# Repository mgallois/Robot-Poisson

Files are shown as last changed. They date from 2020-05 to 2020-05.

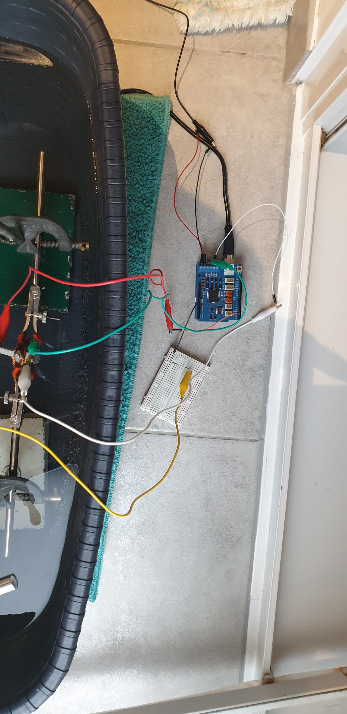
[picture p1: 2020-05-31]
documents tiers/Images/5.jpg

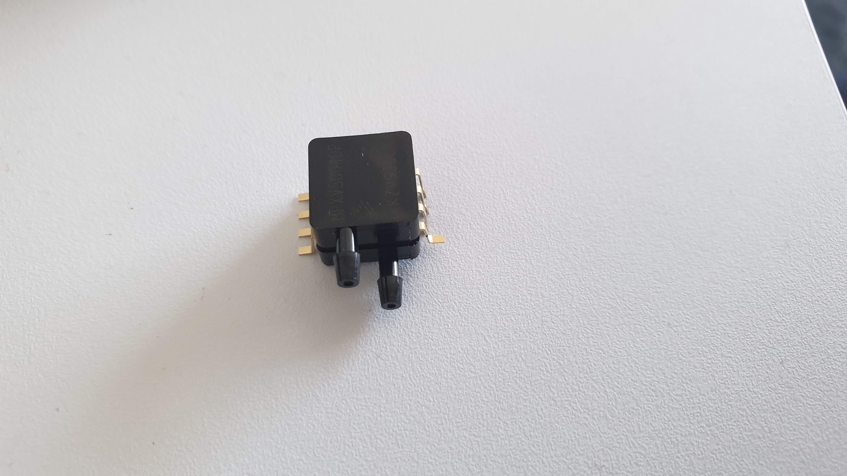
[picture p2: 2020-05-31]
documents tiers/Images/12.jpg

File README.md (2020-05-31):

# Robot-Poisson

INTRODUCTION :

Plusieurs domaines d’applications sont touchés par la nécessité d’entreprendre des prises de vues sous-marines : infrastructures immergées, barrage, pipeline, expertise maritime de bateaux (coques), recherche sous-marine, aquaculture, etc. L’emploi de drones sous-marins a à la fois rendu l’inspection de ces milieux subaquatiques plus simple, rapide et moins coûteuse, et permet d'explorer des fonds marins fragiles sans endommager l'environnement et son écosystème.

Cependant certaines profondeurs sont difficiles d’accès, des engins de faible volume qui embarquent l’énergie nécessaire à la réalisation de leur mission sont alors indispensables. D’où le besoin de systèmes peu énergivore.

Il faut savoir que dans le milieu du XXième siècle, le biologiste Sir James Gray mis en évidence une singularité à qui il donna son nom . Son hypothèse, qui a formé la base de l'analyse énergétique de la nage des dauphins par Gray, était qu'un animal qui nage dépense essentiellement son énergie musculaire pour surmonter la traînée. Or il énonça que la puissance dépensée par un dauphin pour nager à une vitesse donnée peut être sept fois inférieure à celle utilisée par des moteurs pour propulser un corps rigide à la même vitesse, ce qui conduit au paradoxe. [Extrait de sa thèse](https://jeb.biologists.org/content/jexbio/13/2/192.full.pdf).

Ainsi sa conjecture doit être révisé :  la puissance de traînée peut être supérieure à la puissance musculaire sans enfreindre tout principe physique.

Pour expliquer ce phénomène, il faut s’intéresser à la nage du poisson qui fait se propager une onde le long de son corps. On peut associer au déplacement du poisson un nombre de Reynolds correspondant à une allée de tourbillons de Karman. L’action de la queue va déformer cette allée et déplacer les tourbillons de l’autre côté de l’axe de la queue. Cette allée de tourbillons de Karman inversée crée un excès de quantité de mouvement qui entraîne une force propulsive sur le poisson. (Voir [ici](https://github.com/mgallois/Robot-Poisson/blob/master/explication%20rapide%20ph%C3%A9nom%C3%A8ne.md) pour une explication un peu plus détaillé)

Cette démarche biomimétique apparaît prometteuse pour remplacer la traditionnelle hélice de propulsion. L’objet de la robotique biomimétique est de concevoir et fabriquer des machines inspirées de la faune sous-marine, qui ont l’avantage de ne pas effrayer la vie marine contrairement à nos réalisations actuelles. Les premiers prototypes de « robots poissons » sont en développement, voire prêt à la commercialisation tel SoFi conçu par des chercheurs du MIT. C’est un poisson robotique sous-marin non attaché qui peut exécuter de manière autonome des commandes reçues à distance d'un plongeur. Ce projet démontre la possibilité de propulser un drone en imitant la nage d’un poisson.

Notre objectif est de concevoir un robot poisson à la fois souple et adapté à l’immersion. Le poisson robotisé doit se mouvoir à l’aide d’une ondulation biomimétique développant une force de poussée. Il sera question de concevoir, à l’aide de Simon Querat de l’ENS Rennes, un actionneur qui mettra en mouvement une queue moulée en silicone.

Enfin, l’un des défis d’une telle conception est de définir la fonction de déformation de la queue idéale. Son obtention est d’autant plus complexe qu’il fait appel à des notions complexes de mécanique des fluides, dont l’équation de Navier-Stokes qui est non linéaire. Il est cependant possible d’utiliser des modèles informatiques. Ces outils permettent de calculer la résultante des forces s’exerçant sur un corps déformable plongé dans un fluide en écoulement. Le Code utilisé ici est [LilyPad](https://github.com/weymouth/lily-pad).

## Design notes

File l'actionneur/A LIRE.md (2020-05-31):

# Etude de l'actionneur

__Principe de fonctionnement :__

L’objectif est d’agiter la queue du poisson pour qu’ils puisse nager. L’utilisation d’un servomoteur classique nous a semblé compliqué car beaucoup d’entre eux ont un temps de parcourt beaucoup trop long. Nous avons donc décidé d’en concevoir un nouveau :



Comme le montre cette image, l’idée est d’utiliser un aimant permanant qui serait placé à l’intérieur d’une bobine. En faisait circuler un courant dans la bobine, nous créons un couple sur l’aimant. En faisant circuler un courant alternatif, nous pouvons agiter les aimants.

Dans la pratique, nous fixons les aimant dans un cadre imprimé en 3D auquel la queue du poisson pourra venir se fixer :




La commande se fait soit par un montage push pull ([vidéo](https://youtu.be/8bh-lfFtLSA)), soit à l’aide d’une carte arduino ([code](https://github.com/mgallois/Robot-Poisson/blob/master/codes%20divers/code%20arduino/programme_commande_actionneur/programme_commande_actionneur.ino)).

__Mesure du couple transmissible :__

On se propose ici de déterminer expérimentalement le couple transmissible. En effet, nos modèles théoriques sont trop éloignés de la réalité (bobine d’épaisseur non négligeables, champs des aimants irréguliers, etc…).

Afin de mesurer la relation entre le couple et l’intensité, nous accrochons un dynamomètre à l’extrémité de l’actionneur et nous l’alimentons avec un courant continu d’intensité variable. ([Résultats](https://github.com/mgallois/Robot-Poisson/blob/master/l'actionneur/Couple%20Actionneur%20en%20fonction%20de%20l'intensit%C3%A9.xlsx))

__Tracé dans Bode du comportement de l’actionneur :__

L’étude de la réponse se fait par analyse vidéo. Cette étape est pour le moment en suspend.([ebauche tableur](https://github.com/mgallois/Robot-Poisson/blob/master/l'actionneur/trac%C3%A9%20dans%20bode%20(%C3%A9bauche).xlsx)).

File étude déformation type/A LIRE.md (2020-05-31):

INTRODUCTION

Le but de cette étude est de déterminer la géométrie que la queue en silicone devra satisfaire. Concernant la forme globale, il s’agira d’un profil Nacca.

Objectifs :

*	Déterminer les déformations possibles pour une queue déformable agité à son extrémité
*	Simuler à l’aide de Lilypad la poussé de chaque déformation puis déterminer la plus efficace.
*	Estimer les besoins en alimentation de l’actionneur et la taille maximale de la queue pour satisfaire à la déformation choisie et pour atteindre une fréquence de l’ordre de 2 ou 3 Hz.

I_ DETERMINER LES DEFORMATIONS POSSIBLES ET SIMULATION

Nous observons la déformation d’une feuille de papier de fort grammage (300g.m-2) soumise à une excitation sinusoïdale à l’une de ses extrémités :



En fonction de la fréquence, nous obtenons différentes déformation types. Nous pouvons ensuite utiliser Lylipad pour déterminer à quelle vitesse se déplacerait un profil Nacca qui aurait ces déformations. Le profil Nacca utilisé correspond à la forme prévue dans [ce fichier](https://github.com/mgallois/Robot-Poisson/blob/master/Plans/mod%C3%A8le%20de%20queue.SLDPRT).

NB : Comparer directement ces vitesses n’aurait pas beaucoup de sens. En effet, il est évident que plus la fréquence de nage est élevée, plus un poisson ira vite. C’est pourquoi dans la simulation nous ne changeons pas la fréquence de la nage, mais seulement la déformation en elle-même. Par défaut, nous appliquons une fréquence de 3Hz à la simulation.

[vidéo de l'expérience](https://github.com/mgallois/Robot-Poisson/blob/master/%C3%A9tude%20d%C3%A9formation%20type/vid%C3%A9o%20d%C3%A9formation.mp4) (fréquence de 1Hz à 15Hz avec un pas de 1Hz toute les 10 secondes).

| Fréquence d’agitation de la feuille de papier (en Hz) | Vitesse simulée Avec lilypad (en cm.s-1) |
| :---:| :---: |
|1|0,6|
|2|1,2|
|3|1,0|
|4|0,9|
|5|1,0|
|6|0,8|
|7|0,8|
|8|0,7|
|9|0,6|
|10|0,6|
|11|0,5|

Nous obtenons ainsi un objectif de déformation à atteindre.

Une seconde simulation montre que plus la queue est grande, plus la propulsion est efficace. Nous chercherons donc à avoir la plus grande queue possible.

II_ BESOINS EN ALIMENTATION ET TAILLE MAXIMALE
	 
HYPOTHESE 1 : L’épaisseur de la queue influe peut sur le couple résistant devant la surface exposée : on peut donc utiliser une plaque de même surface que la queue.

HYPOTHESE 2 : Au vue de la déformation choisie, une plaque de PVC légèrement déformable apporte une estimation suffisamment proche du couple résistant. 

Les plaques en PVC correspondent aux différentes tailles de queue envisagées. Nous ne nous attarderons pas sur des calculs d’inertie, de couple résistant, etc. Comme nous cherchons à atteindre une fréquence de l’ordre de 2 ou 3 Hz, nous allons mesurer le temps de réponse à un échelon pour coup de nageoire.

Nous allons mesurer le temps de réponse à un échelon pour un battement en fonction de l’intensité fournie à l’actionneur et de la taille de la plaque en PVC. Nous utilisons des plaques de PVC de différentes tailles aillant la forme d’une queue de poisson pour simuler la présence d’une queue. La mesure se fait avec une carte Arduino. La mesure du temps se fait entre le début de la consigne et l’établissement du courant à travers la tige de cuivre (assimilable à un contacteur).

Montage sans plaque de PVC :





Code Arduino [ici](https://github.com/mgallois/Robot-Poisson/blob/master/codes%20divers/code%20arduino/code_calcul_Cr/code_calcul_Cr.ino).

Les plaques de PVC sont identifiées par leur longueur noté h.

Résultat de l’expérience :



NB : le point h=0 correspond à la valeur à vide, c’est-à-dire sans plaque de PVC.

Pour l’intensité maximale (2500 mA), on peut obtenir la fréquence maximale en fonction de h(mm) :



Nous chercherons donc à fabriquer une queue d’environ 9cm.

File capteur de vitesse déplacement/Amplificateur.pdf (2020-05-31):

Amplificateur

Problème :

le capteur de pression différentielle fournit une image de la pression sur une plage de 25mv (pression entre 0 et 10kPa et pente de 2.5mv/kPa). Or, l’Arduino mesure sur une plage de 5V.

Solution :

Amplificateur différentielle :

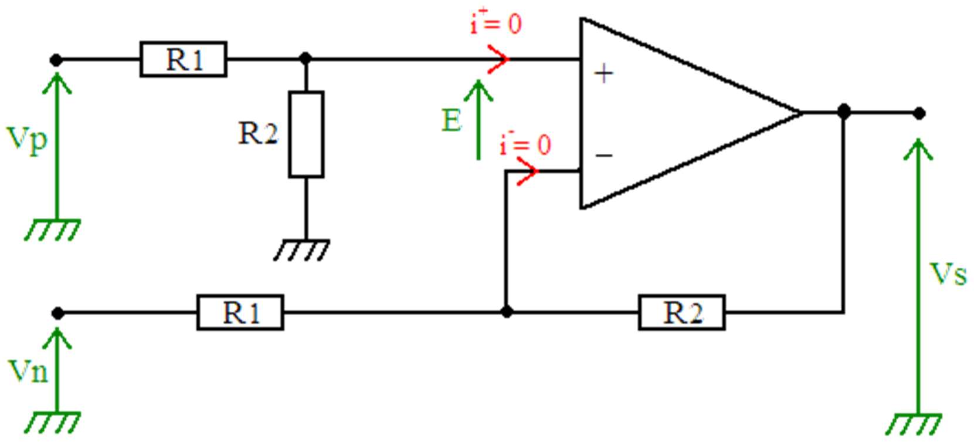
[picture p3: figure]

Vs = (Vp − Vn) ×

R2
R1
Echantillonnage de l’Arduio : 1024

Notre plage de mesure : de 0Pa à 200Pa

200 Pa correspond à 0.5mv

Il nous faudrait :

- Un amplificateur différentiel pour passer de 0.5mv à 5V
- Une sécurité s’assure que la tension ne soit pas supérieure à 5V en entré de l’arduino

L’amplificateur : x10⁴

### 1 amplificateur différentiel et deux montage amplificateur inverseur

Montage différentiel : R1=200Ohm, R2=2KOhm => amplification *10

Amplificateur inverseur 1 : R1=200Ohm, R2=2KOhm => amplification *-10

Amplificateur inverseur 2 : R1=200Ohm, R2=20KOhm => amplification *-100

TT amplification * 10 000

La sécurité :

Montage de régulation de tension (labo)

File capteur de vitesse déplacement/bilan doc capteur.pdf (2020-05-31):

Type | MPXV5004DP
Branchement | SMD
Modèle | pression différentielle
Signal de sortie (min.) | 0 V
Sortie de signal max. | 4.9 V
Gamme de mesure (pression) minimale | 0 kPa
Gamme de mesure (pression) (max.) | 3.92 kPa
Plage de mesure (pression) | 0 kPa à 3.92 kPa
Tension de fonctionnement min. | 4.75 V/DC
Tension de fonctionnement max. | 5.25 V/DC
Tension de fonctionnement | 4.75 - 5.25 V/DC
Température min. | 0 °C
Température max. | +85 °C
Type | MPXV5004DP
Type de produit | Capteur de pression

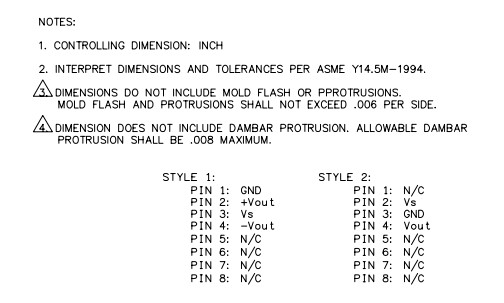
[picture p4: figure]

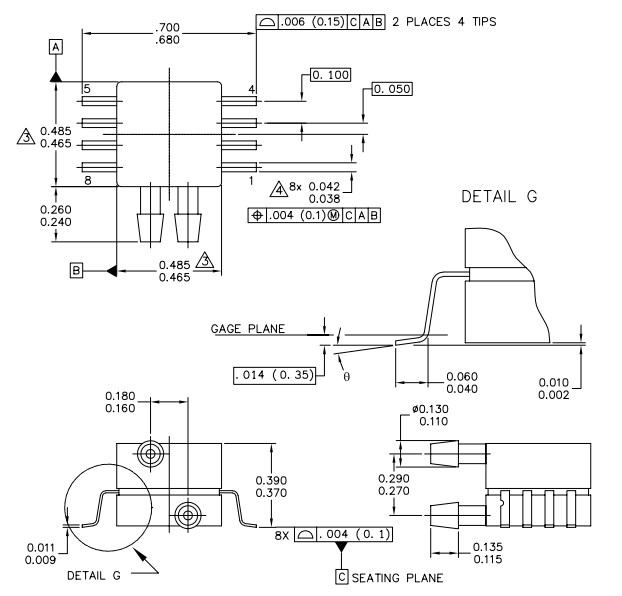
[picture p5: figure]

Note : 0.13inch = 3.302mm

1inch = 25.4 mm

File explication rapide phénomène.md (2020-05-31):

Un poisson ressemble souvent au profil NACA (aile d’avion) qui est la forme la plus adaptée au déplacement dans un fluide (forme qui a le coefficient de traînée le plus faible (Cx(NACA)≈0.04).

Un poisson se déplace en propageant le long de son corps une onde longitudinale, et donc la nageoire dorsale. Lorsque celle-ci est mise en oscillation périodique, cela joue sur les schémas de tourbillons observés dans le sillage. A partir d’une certaine amplitude d’oscillation seuil, on peut observer une inversion du sens de rotation des tourbillons créés dans le sillage par rapport au cas statique.



Dans le cas statique, un bilan de la vitesse moyenne de l’écoulement montrera que la présence du sillage tourbillonnaire est associée à une diminution de la vitesse moyenne de l’écoulement, ce qui est caractéristique d’une force de trainée sur la nageoire fixe. 

Par contre, dans le cas où l’oscillation de la nageoire a permis l’inversion du sens de rotation des tourbillons par rapport au cas statique, on pourra constater que la vitesse moyenne de l’écoulement au niveau du sillage tourbillonnaire présente une augmentation de la vitesse moyenne de l’écoulement. Ce jet de vitesse derrière la nageoire en mouvement est la signature d’une force de propulsion agissant sur la nageoire.

Ainsi, les poissons (mais aussi les oiseaux, certains insectes,…) savent tirer parti de la production des tourbillons qu’ils génèrent en battant des nageoires : alors que ceux-ci pourraient les freiner, ils s’arrangent pour les déplacer de l’autre côté du sillage tourbillonnaire d’un coup de nageoire.

Le problème avec les travaux de Gray est donc qu’il travaillait avec l’hypothèse de corps inertes et donc sans diminution de l’effort de trainée.

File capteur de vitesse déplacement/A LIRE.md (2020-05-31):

# Capteur de vitesse

INTRODUCTION :

L’objectif de cette partie est de réaliser un capteur de vitesse du poisson. Ce capteur a plusieurs intérêts. Dans un premier temps il servira à prendre la vitesse du poisson afin de pouvoir réaliser des mesures sur l’efficacité de la queue, du rendement, etc. Dans un second temps, il servira à asservir le poisson en vitesse. En effet il peut être intéressant, selon la mission du drone, de pouvoir contrôler sa vitesse. (Mesures de distances sans dépondre de la technologie GPS qui fonctionne mal sous l’eau, mesure de courant marin, vitesse adéquat à l’observation de certains milieux en autonomie, …)

Principe :

Au vu de la vitesse faible du poisson nous nous dirigeons vers un capteur de pression différentiel (tube de Pitot). En voici le principe :



Au début, nous ne disposions pas de tube de Pitot adéquat et pour rendre facile la communication avec une carte arduino nous avons commencé par utiliser un capteur de pression différentiel placé dans un capsule étanche.

Capteur :





[Code pour l’utilisation](https://github.com/mgallois/Robot-Poisson/blob/master/codes%20divers/code%20arduino/capteur_pression/capteur_pression.ino)

Doc capteur : [résumé](https://github.com/mgallois/Robot-Poisson/blob/master/capteur%20de%20vitesse%20d%C3%A9placement/bilan%20doc%20capteur.pdf)
 / [complète](https://github.com/mgallois/Robot-Poisson/blob/master/documents%20tiers/fiche-technique-1182924-capteur-de-pression-nxp-semiconductors-mpxv5004dp-0-kpa-a-392-kpa-smd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)

[Circuit entre le capteur de l’arduino](https://github.com/mgallois/Robot-Poisson/blob/master/capteur%20de%20vitesse%20d%C3%A9placement/Amplificateur.pdf)

Montage :






Les premiers tests semblent bien renvoyer un résultat linéaire lorque la variation de pression est due à une variation de la profondeur sous l'eau. Les tests à venir devraient permettre de déterminer une loi entre la vitesse de déplacement de la capsule et la différence de pression mesurée.

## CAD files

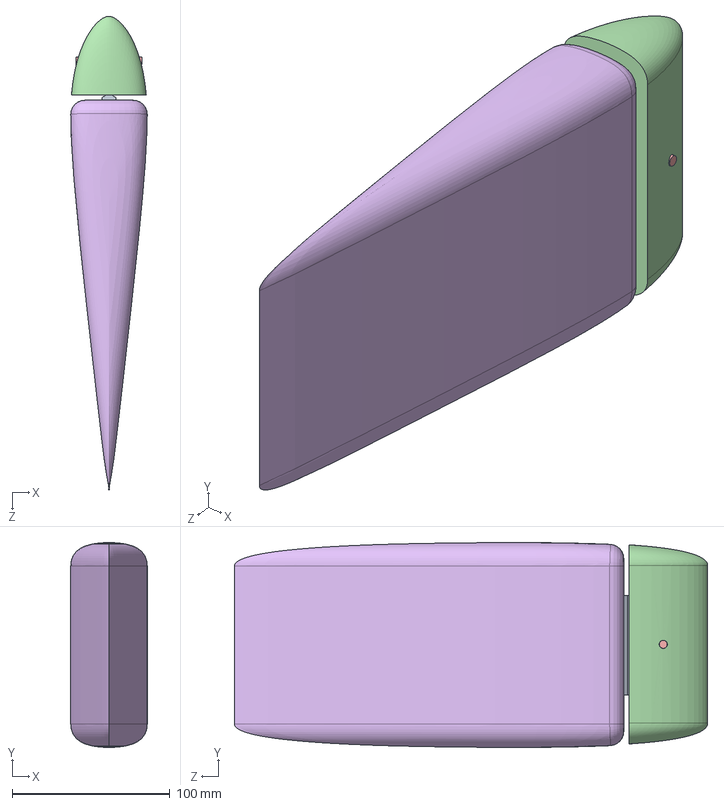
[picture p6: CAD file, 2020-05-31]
Plans/Solidworks/Assemblage Actionneur.SLDASM
48.6 x 130.0 x 300.2 mm
Actionneur Aimant
Actionneur bobine
Tige x 2
Tête entière
Goupille tête actionneur aimant
Queue entière

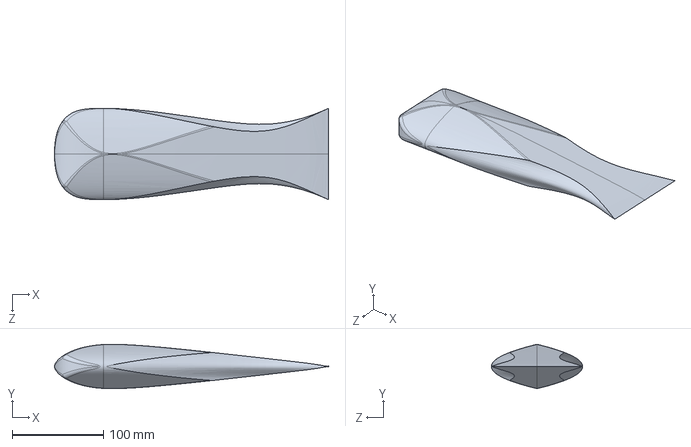
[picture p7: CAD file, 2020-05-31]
Plans/modèle de queue.SLDPRT
300.0 x 48.5 x 100.0 mm

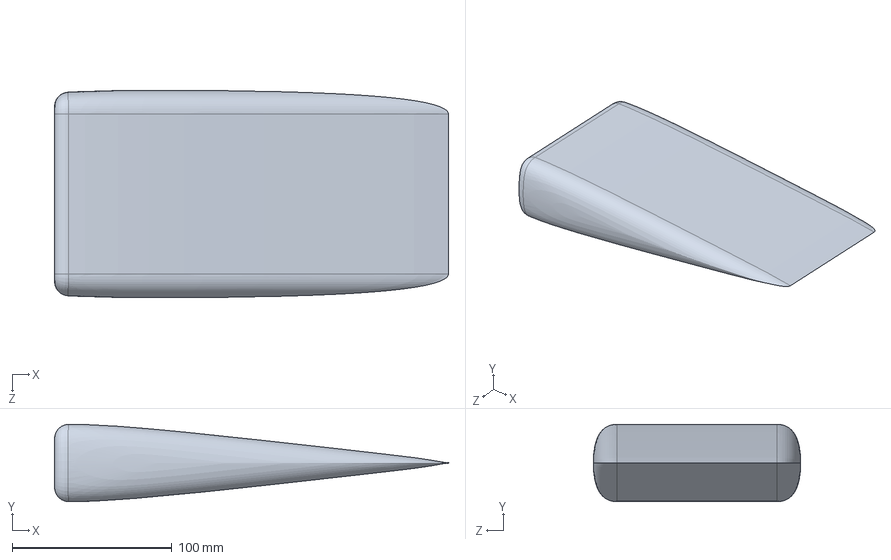
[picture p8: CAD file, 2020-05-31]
Plans/Solidworks/Queue entière.SLDPRT
247.0 x 48.6 x 130.0 mm

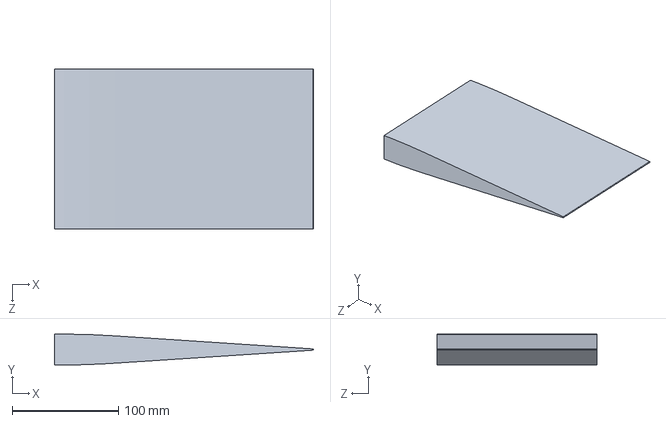
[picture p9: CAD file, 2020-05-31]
Plans/Solidworks/Tête.SLDPRT
243.6 x 29.0 x 150.0 mm

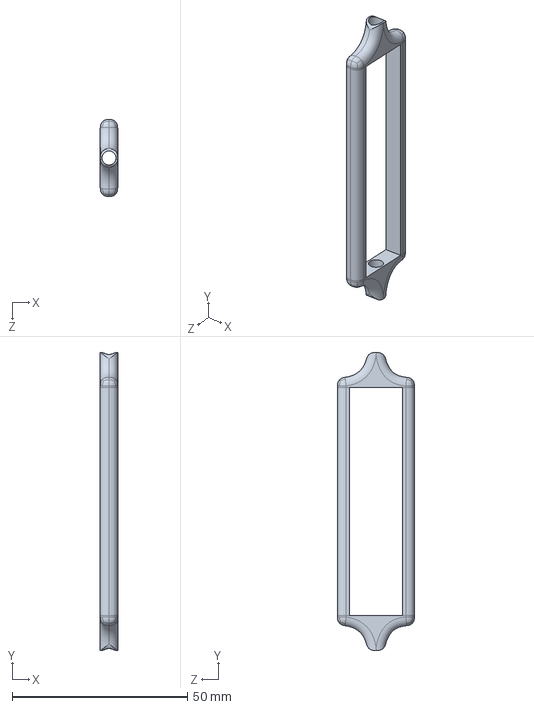
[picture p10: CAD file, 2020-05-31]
Plans/Solidworks/Actionneur bobine.SLDPRT
5.00 x 85.0 x 22.0 mm

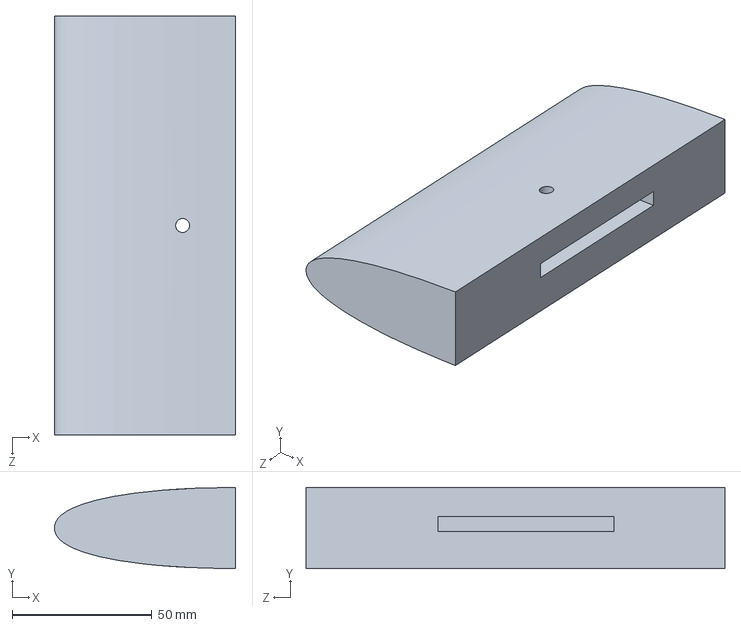
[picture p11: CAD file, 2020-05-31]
Plans/Solidworks/Tete poisson.SLDPRT
64.9 x 29.1 x 150.0 mm

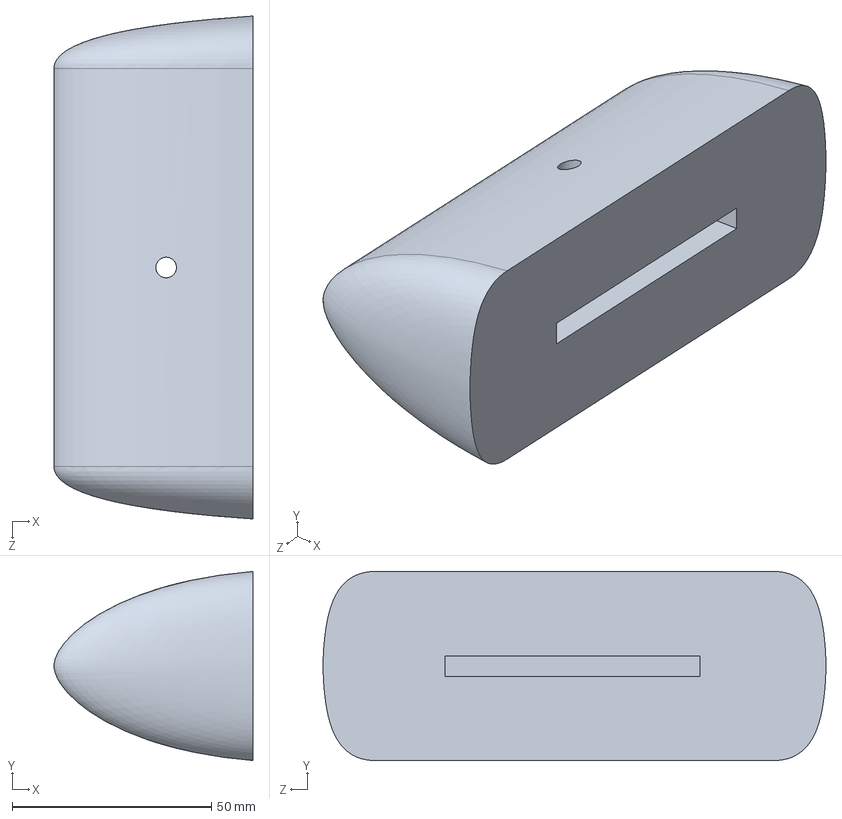
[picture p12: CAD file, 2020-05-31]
Plans/Solidworks/Tête entière.SLDPRT
50.0 x 47.5 x 126.4 mm

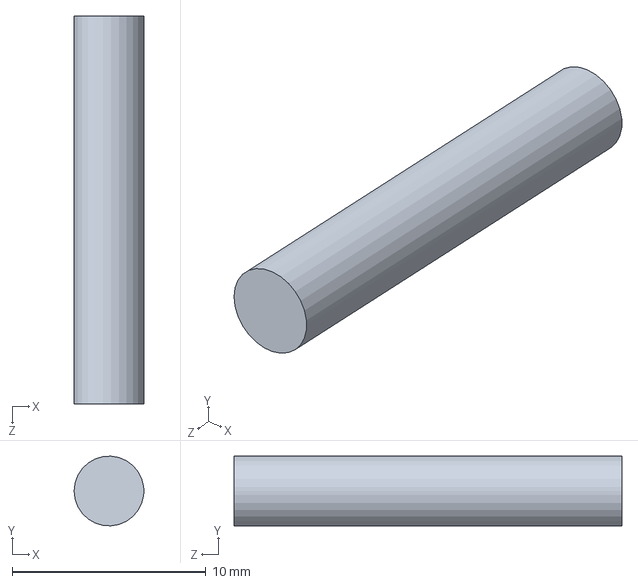
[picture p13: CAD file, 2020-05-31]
Plans/Solidworks/Tige.SLDPRT
3.60 x 3.59 x 20.0 mm

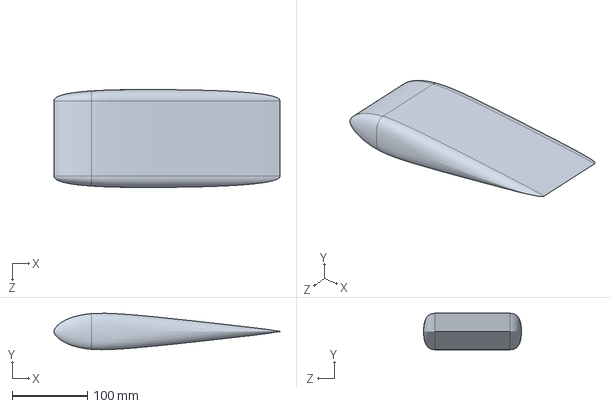
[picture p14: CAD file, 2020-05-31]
Plans/Solidworks/Corps entier.SLDPRT
300.0 x 48.5 x 130.0 mm

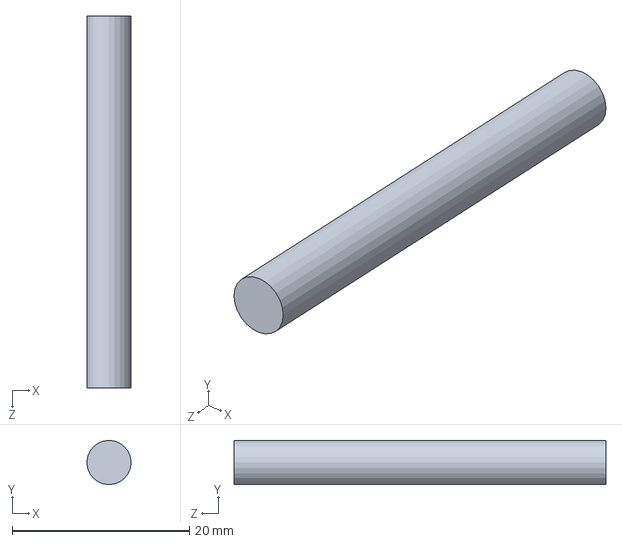
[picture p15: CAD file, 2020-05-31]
Plans/Solidworks/Goupille tête actionneur aimant.SLDPRT
5.00 x 5.00 x 42.0 mm

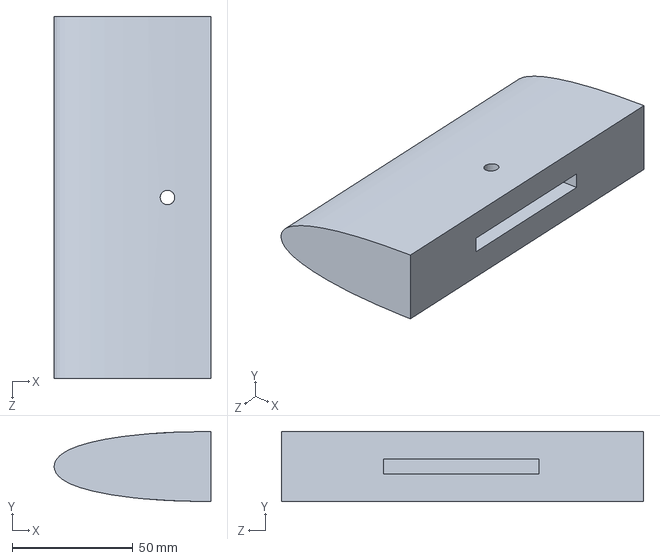
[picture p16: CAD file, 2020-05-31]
Plans/Solidworks/Poisson entier.SLDPRT
64.9 x 29.1 x 150.0 mm

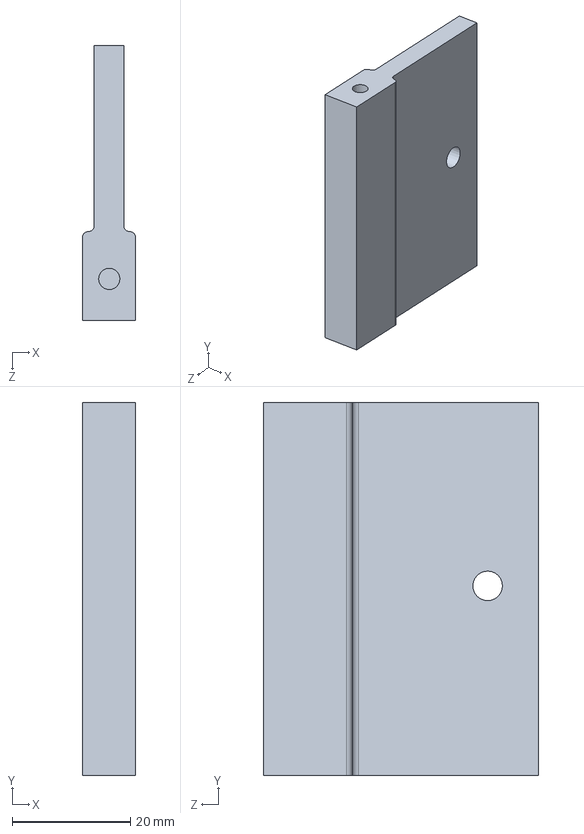
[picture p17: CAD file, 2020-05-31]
Plans/Solidworks/Actionneur Aimant.SLDPRT
9.00 x 63.0 x 46.4 mm

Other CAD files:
Plans/Solidworks/Corps entier modifié.SLDPRT
Plans/Solidworks/Tête poisson.SLDPRT
Plans/Assemblage Actionneur.x_t
Plans/Solidworks/Actionneur Aimant.x_t
Plans/Solidworks/Corps entier modifié.x_t
Plans/Solidworks/Poisson entier.x_t
Plans/Solidworks/Tête.x_t

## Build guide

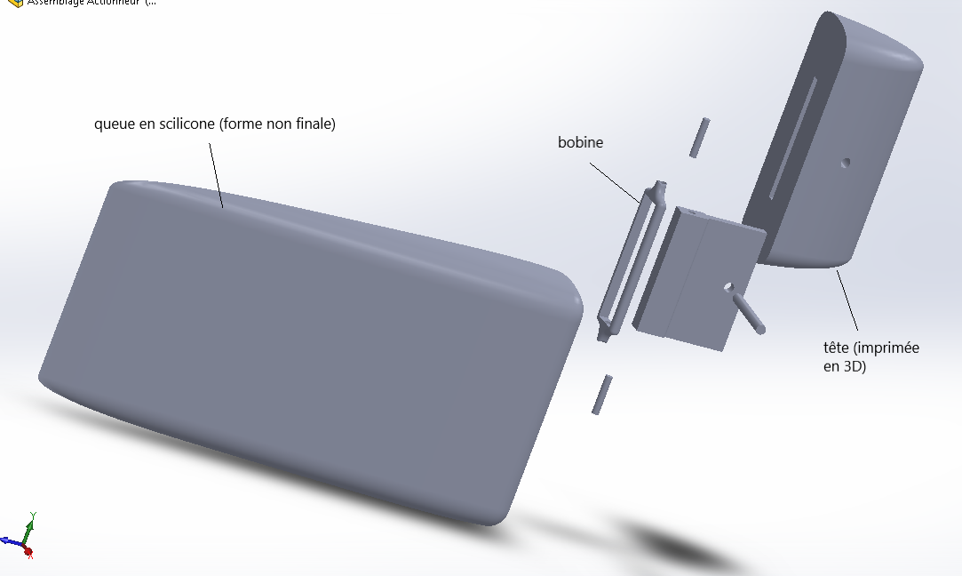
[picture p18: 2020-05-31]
Plans/vue éclaté de l'assemblage.PNG

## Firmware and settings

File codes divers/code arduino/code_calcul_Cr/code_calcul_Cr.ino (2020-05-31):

int P;
boolean contact;
int lecture;

  unsigned long tempsDebut;
  unsigned long tempsFin;


void setup() {
  //Setup Channel A
  pinMode(12, OUTPUT); //Initiates Motor Channel A pin
  pinMode(9, OUTPUT); //Initiates Brake Channel A pin

  P=50;// P entre 0 et 255
  contact=false;

  lecture = 2;
  pinMode(lecture,INPUT_PULLUP);
  Serial.begin(9600);

  // Mise en position initial
  digitalWrite(12, LOW); //Establishes backward direction of Channel A
  digitalWrite(9, LOW);   //Disengage the Brake for Channel A
  analogWrite(3, P);   //Spins the motor on Channel A 
  delay(1000);

  contact=not(digitalRead(lecture));

  delay(1000);
  tempsDebut = millis();

  
}

void loop() {

  if (contact){
    digitalWrite(12, HIGH); //Establishes forward direction of Channel A
    digitalWrite(9, LOW);   //Disengage the Brake for Channel A
    analogWrite(3, P);   //p entre 0 et 255
  }
  else{
    tempsFin=millis();
    Serial.println(tempsFin-tempsDebut);
  }
  contact=not(digitalRead(lecture));
}

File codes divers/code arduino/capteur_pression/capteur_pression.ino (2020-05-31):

int pinPot=0; //variable pour définir le CAN où est connecté le potentiomètre
int valPot=0; //variable pour récupérer la tension aux bornes du potentiomètre traduite par le CAN . On l’initialise à 0.
void setup() {
  Serial.begin(9600); //Initialisation de la communication avec la console
}

void loop() {
  valPot=analogRead(A0); //lit la tension, la convertit en valeur numérique et la stocke dans valeurPot
  Serial.print("Valeur lue : ");
  Serial.println(valPot);
  delay(100);
}
